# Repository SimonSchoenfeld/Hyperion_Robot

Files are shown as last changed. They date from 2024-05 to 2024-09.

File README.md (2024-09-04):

# Hyperion Roboter
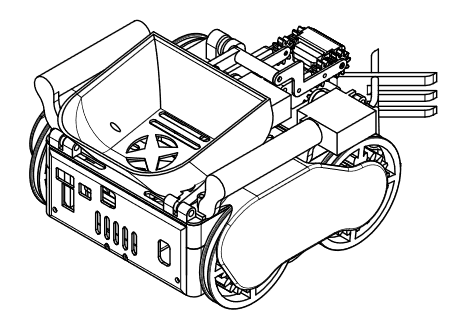
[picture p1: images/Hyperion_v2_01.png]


<br>
Dieses Repository enthält die Dokumentation des Hyperion Roboters, <br>
welcher von Simon Schönfeld für den Robocup Rescue Line Wettbewerb 2024 gebaut wurde. 

## Inhaltsübersicht
1. [Über mich](#über-mich)
2. [Regeln des Robocups](#regeln-des-robocups)
3. [Vorheriger Roboter](#vorheriger-roboter)
4. [Planung Hyperion v2](#planung-hyperion-v2)
   - [Platinen](#platinen)
   - [Das Fahrwerk](#das-fahrwerk)
   - [Das Gehäuse](#das-gehäuse)
   - [Die Kamera](#die-kamera)
   - [Schleifkontakte](#schleifkontakte)
   - [Greifarm](#greifarm)
5. [Funktionen](#funktionen)
   - [Linefollowing](#linefollowing)
   - [Kreuzungen](#kreuzungen)
   - [Hindernisse](#hindernisse)
   - [Rescue Area](#rescue-area)
6. [Probleme](#probleme)
7. [Fazit](#fazit)
8. [Zusätzliche Ressourcen](#zusätzliche-ressourcen)

## Über mich
Mein Name ist Simon Schönfeld, ich besuchte seit der 5ten Klasse die Informatik AG meiner Schule. Ziel dieser AG war es, Lego Roboter zu bauen, welche einer Linie folgen, um mit diesen dann einmal im Jahr beim Robocup Wettbewerb teil zu nehmen. 
Obwohl ich es nie geschafft habe, mich mit einem Lego Roboter für die deutschen Meisterschaften des Robocup zu qualifizieren, beschloss ich mich während der Coronapause gemeinsam mit meinem damaligen Teamkameraden, dazu, einen eigenen Roboter zu bauen. 

## Regeln des Robocups
Die Roboter beim Robocup müssen einen Parkour absolvieren, welcher aus einer Schwarzen Linie und einer "Rescue Area" besteht. Der Roboter muss der Schwarzen Linie folgen und dabei verschiedene Hindernisse überwinden. Diese Hindernisse bestehen aus Bumpern, Blockaden und Lücken. An Kreuzungen befinden sich zudem grüne Maskierungen, welche die Roboter erkennen und abhängig von der Position des Punktes drehen müssen. Die Rescue Area wird mit einem Silbernen Streifen eingeleitet. In ihr kann der Roboter Kugeln in verschiedene Ecken befördern, um Zusatzpunkte zu bekommen. Schwarze Kugeln müssen in die rote Ecke, die Silbernen Kugeln müssen in die grüne Ecke.

Die genauen Regeln befinden sich [hier](https://junior.robocup.org/wp-content/uploads/2024/04/RCJRescueLine2024-final-1.pdf).
<br>
<br>
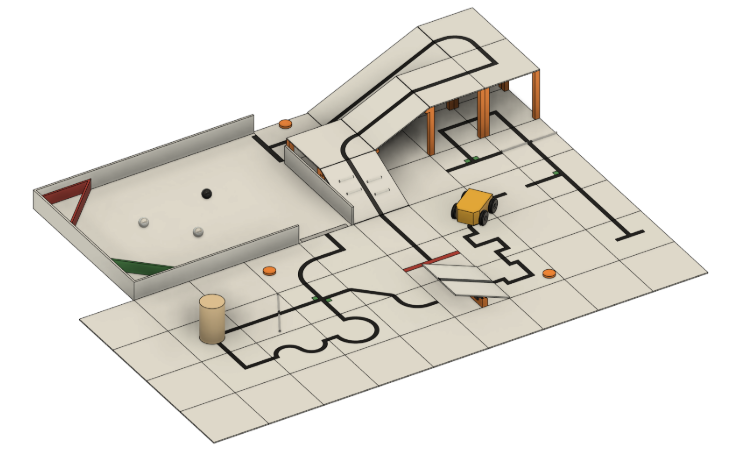
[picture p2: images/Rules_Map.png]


## Vorheriger Roboter
Obwohl ich es nie geschafft habe, mich mit einem Lego Roboter für die deutschen Meisterschaften des Robocup zu qualifizieren, beschloss ich mich während der Coronapause gemeinsam mit meinem damaligen Teamkameraden, dazu, einen eigenen Roboter zu bauen. Zu diesem Zeitpunkt war ich zwischen 14 und 15 Jahre alt und wusste so gut wie gar nichts über Elektronik und dem Erstellen von 3D Modellen, lediglich mit dem Programmieren hatte ich mich bereits länger beschäftigt. 
Da sich zu der Zeit auch Niemand in der AG damit auskannte, waren wir mehr oder weniger auf uns alleine gestellt und brauchten bereits mehrere Monate um zum ersten Mal zwei Schrittmotoren zu verwenden. Ich nahm den Roboter mehrfach mit nach Hause und baute und testete ihn dort ausgiebig. 
Als wir schließlich mit dem Roboter angetreten sind, versagte er vollkommen auf Grund von vielen unterschiedlichen Problemen. Dennoch habe ich in diesem Jahr so viel gelernt wie nie zuvor und beherrschte nun Grundkenntnisse in Schaltkreisen, 3D modellieren mit Fusion 360 und der Gesamtmechatronik eines Roboters. Da der Roboter meinem Teammitglied über die Zeit deutlich zu komplex und zeitintensiv wurde baute und programmierte ich ihn fast vollständig alleine und nach dem Wettbewerb verließ er die AG.

>[!NOTE]
> Wenn es darum geht im Robocup zu gewinnen, ist das Bauen eines eigenen Roboters absolut kontraproduktiv. Die Lego Roboter sind inzwischen so ausgereift, dass sie um Welten genauer und simpler sind. Die Gewinner des Robocups sind fast ausschließlich Lego Roboter und auch in den Qualifikationsrunden, an denen ich teilgenommen habe bin ich bis jetzt immer der Einzige Teilnehmer mit einem 100% selbstgebauten Roboter gewesen. Ich baue dennoch einen eigenen Roboter, da es mir nicht um das Gewinnen, sondern um die Herausforderung geht und darum, neue Dinge zu lernen. 

## Probleme des ersten Roboters

- Der Roboter basierte auf einem Fahrwerk eines Schülers, welcher schon vor mehreren Jahren die Schule verlassen hatte. Er hat sich damals mit seinem selbstgebauten Roboter für die deutsche Meisterschaft qualifizieren können. Der Roboter befand sich zu großen Teilen noch im Besitz der AG, weshalb wir das Fahrwerk als Grundbaustein nutzen und über die Zeit immer weiter veränderten. Am Ende war zwar nur noch die verwendete Kette ein Originalteil, dennoch haben wir die Ursprungsmaße nie verändert. Der Roboter war zu klein und Schmal, um noch mehr Bauteile unter zu bringen. Somit bestand der Roboter lediglich aus den Motoren und Treibern, sowie den Farbsensoren, Arduino und Akku. Später fügten wir zudem ein Greifarm hinzu.
<br>
<br>


- Aufgrund der Bauweise war es sehr schwierig an das Innere des Roboters zu kommen, weshalb man ihn ständig auseinander bauen musste. Die Kabel waren zudem alle weiß und rot, was schnell zu Verwirrung führte. Der später hinzugefügte Greifarm war sehr schlecht konstruiert und passte nicht wirklich zum Fahrwerk. All dies führte dazu, dass das Finden und Beheben von Fehlern sehr zeitaufwändig gewesen ist. Zudem gab es keine Möglichkeiten die Kugeln überhaubt zu finden oder die Rescue Are überhaubt zu lokalisieren. 
<br>
<br>
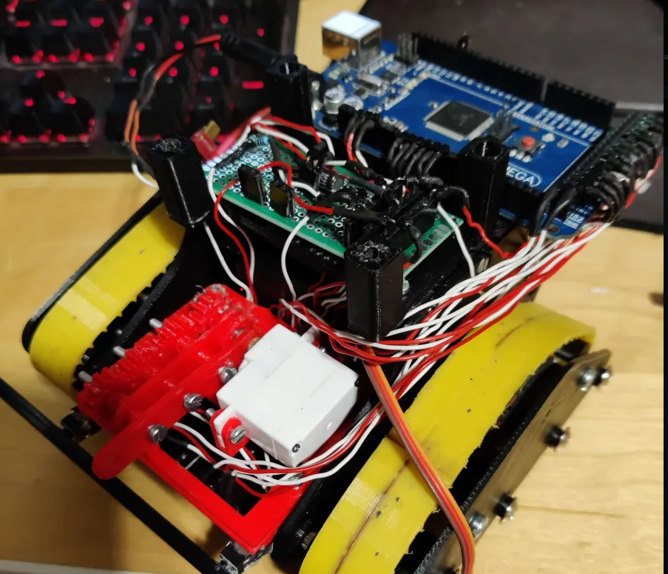
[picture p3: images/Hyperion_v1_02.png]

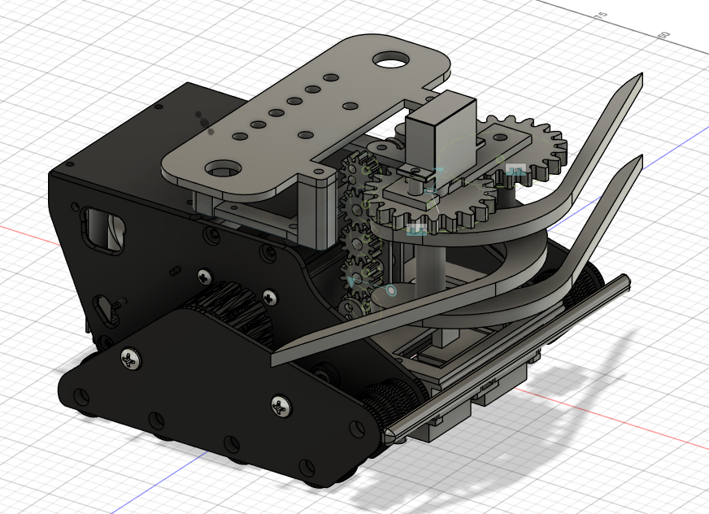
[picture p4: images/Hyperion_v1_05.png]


- Die Kette war nicht rutschfest genug, wodurch der Roboter auf Steigungen wiederholt abrutschte. Die Räder unter den Ketten haben sich zu dem bei zu großer Belastung selber festgezogen und sind regelmäßig blockier, da sie auf Schrauben montiert waren. Die hohe Anzahl an kleinen Bauteilen hat zudem dafür gesorgt, dass an dem kleinen Roboter über 100 Schrauben verbaut waren. Dies machte ihn sehr schwer. Dieses Problem und dadurch, dass die Schrittmotoren sehr ineffizient angesteuert wurden, sorgte dafür, dass der Roboter sich kaum bewegen konnte. 
<br>
<br>
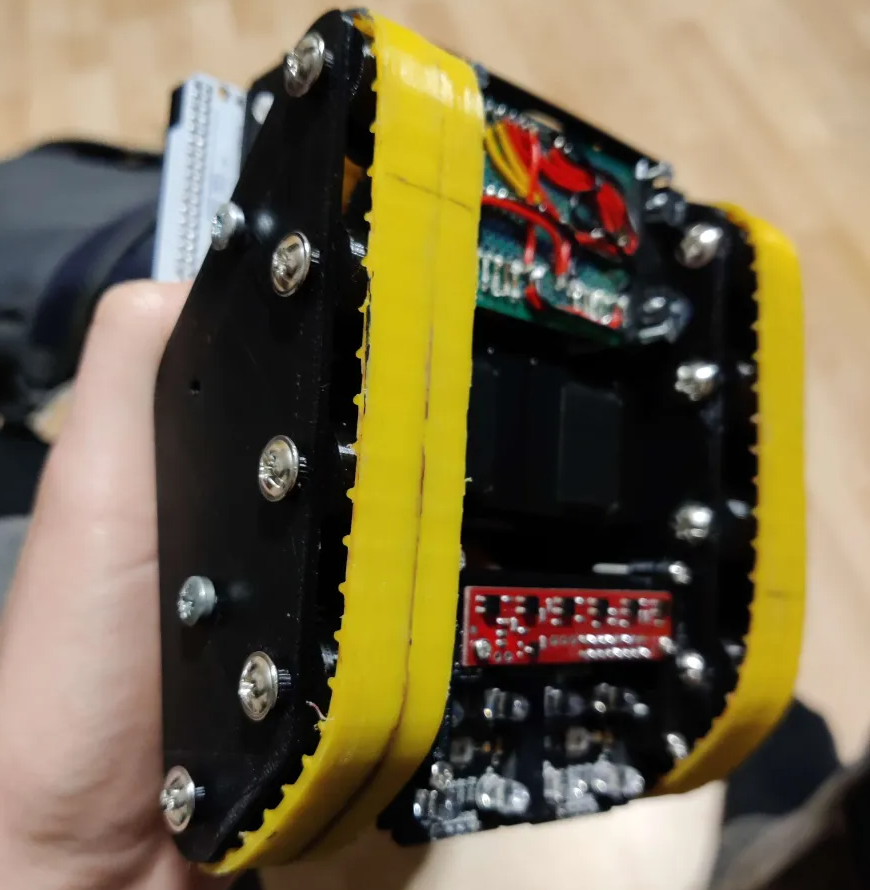
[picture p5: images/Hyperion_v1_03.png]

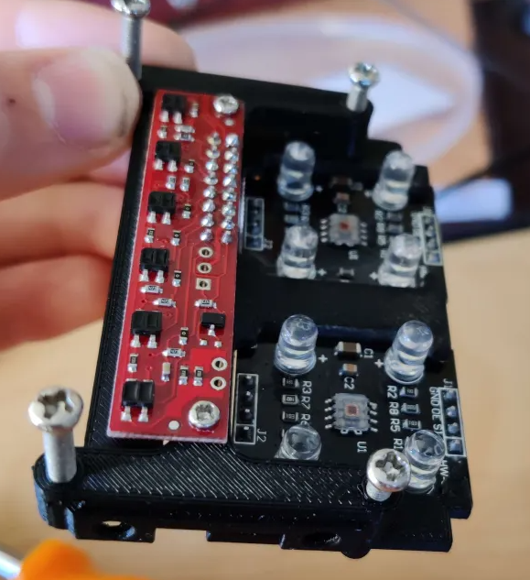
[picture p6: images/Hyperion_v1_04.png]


- Wenn es darum ging einer einfachen Linie zu Folgen hat der Roboter sehr präzise funktioniert. Dennoch gab es immer wieder Probleme welche schnell dazu führten, dass der Roboter gar nicht mehr funktionierte. Und auch das Erkennen der Kreuzungen funktionierte nur selten, da die Farbsensoren zu ungenau waren und sehr genau kalibriert werden mussten. (Dies liegt auch an dem speziellen Grünton der Punkte)
<br>
<br>

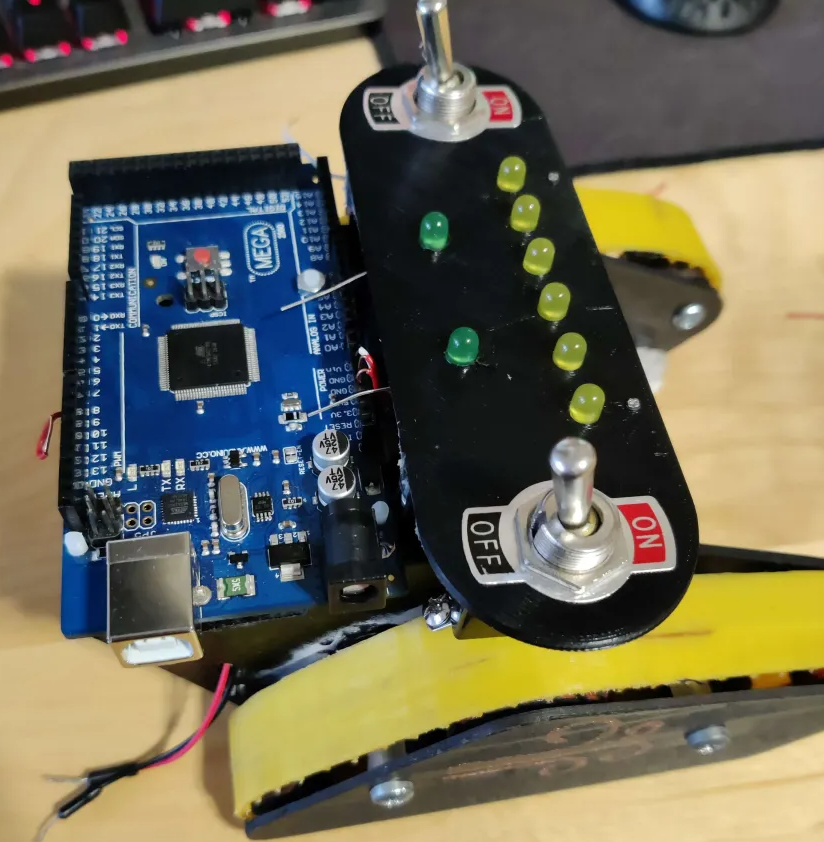
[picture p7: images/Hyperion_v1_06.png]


<br>
<br>
<br>

# Planung Hyperion v2
<br>

## Platinen
Statt einem Arduino Mega soll nun ein Raspberry Pi verwendet werden. Dieser ermöglicht es eine Kamera zu verwenden, um die Kugeln zu finden. Zudem ermöglicht er das Nutzen von Multiprozessen. Zudem kann der Roboter nun kabellos programmiert werden und ist insgesamt leistungsfähiger. Damit der Roboter einfach auseinandergebaut werden kann bedarf es mehrer Platinen, welche verschiedene Aufgaben erfüllen. Diese Platinen sind wiederum mit angesteckten Kabeln verbunden. Somit sind keine Bauteile permanent miteinander verbunden und lassen sich leicht zerlegen. 

### Analog-Digital-Wandler
Da die Grünen Punkte an den Kreuzungen durch die Kamera erkannt werden können, benötigt der Roboter lediglich die Grayscalesensoren zum Erkennen der Linie und ein Ultraschallsensor, welcher Hindernisse auf der Fahrbahn erkennen soll. Leider kann der Raspberry Pi die analogen Werte der Farbsensoren nicht selber auslesen, wie es der Arduino getan hat. Aus diesem Grund wird ein Analog zu Digital Wandler benötigt. Genutzt werden zwei MCP3008 Chips mit je 8 Inputs. Diese können über den SPI Bus mit dem Raspberry Pi verbunden werden und befinden sich auf der ersten Platine. Da die Anzahl an Analogen Inputs nicht mehr von den Anschlüssen des Raspberry Pis abhängig ist, sondern rein von der Anzahl an Wandlern, können gleich zwölf Grayscale Sensoren verwendet werden, wobei trotzdem noch vier Anschlüsse offenbleiben. Eine hohe Anzahl an Sensoren ermöglicht es die Linie in einer großen Fläche lokalisieren zu können. Zudem wird der Einfluss eines einzelnen, eventuell fehlerhaften Sensors reduziert. 
<br>
<br>
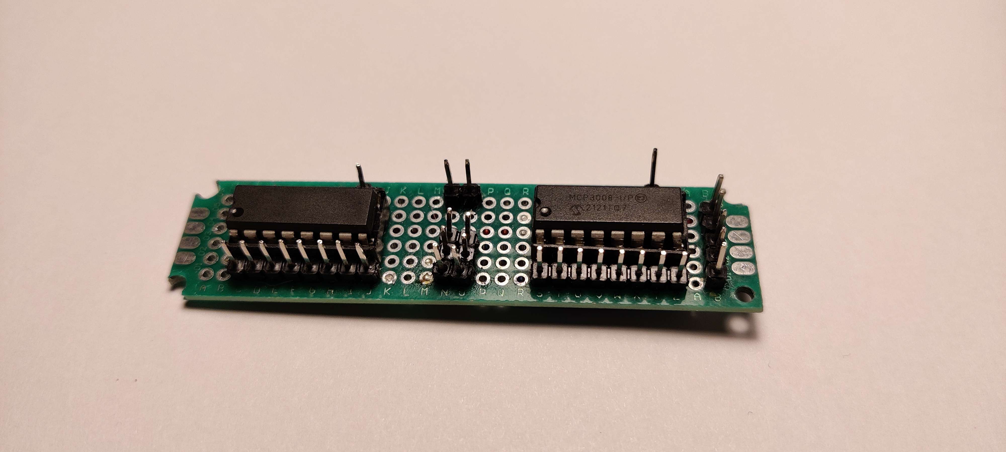
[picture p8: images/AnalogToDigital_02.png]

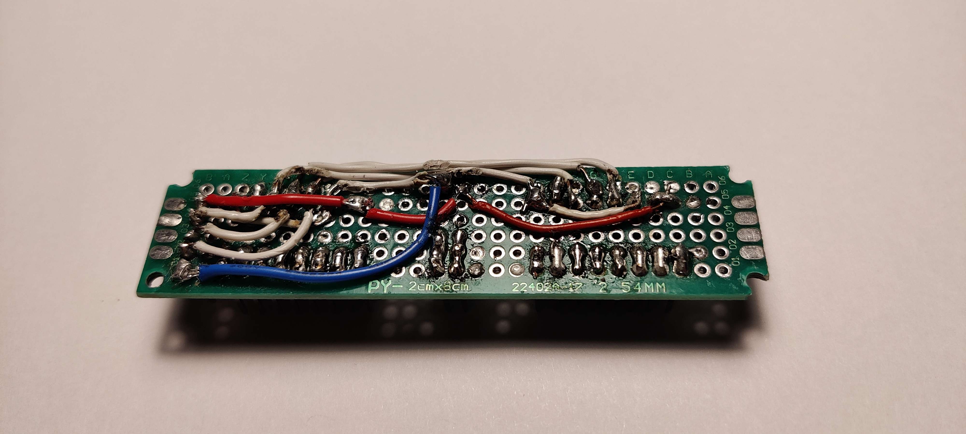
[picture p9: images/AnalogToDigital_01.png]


### Stromversorgung
Für die Schaltung werden zwei verschiedene Spannungen benötigt. 12V für die Motoren und 5.1V für den Raspberry Pi. Der Raspberry Pi hat zudem einen 3.3V Pin-Ausgang. Als Stromquelle wird ein 3S 12V LiPo Akku verwendet. Ein Aufwärtswandler bringt diese 12V auf 5.1V, welche über eine Verteilerplatine auf ein USB-Slot geleitet werden. Über ein kurzes USB-Kabel kann so der Raspberry Pi versorgt werden. Wenn man ein externes USB-Kabel verwendet, kann der PI auch angeschaltet und programmiert werden ohne dass die Motoren verbunden sind. An dem Akku befindet sich zudem ein Schalter, um den gesamten Strom abzuschalten und ein Modellflugzeug-Alarm, damit der Akku nicht vollständig entladen wird (und kaputt geht). 
<br>
<br>
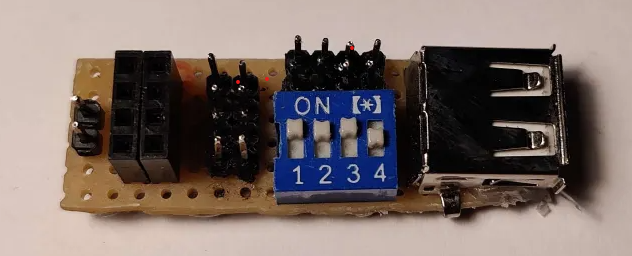
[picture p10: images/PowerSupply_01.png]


### Motortreiber
Um die Schrittmotoren ordnungsgemäß bedienen zu können bedarf es an einem Motortreiber für jeden Motor. Um diese Treiber richtig verwenden zu können müssen sie richtig verkabelt werden. Diesen vergleichsweisen komplexen Schaltkreis hatte ich zu Beginn des Projektes noch wie alle anderen Platinen von Hand gelötet. Als ich jedoch schließlich von "a4988" Treibern auf "drv8825" Treiber umgestiegen bin, musste ich eine Änderung an dem Schaltkreis vornehmen. Da die Platine nicht besonders gut verlötet war und die Rückseite der Platine bereits sehr unordentlich geworden ist, entschied ich mich für eine neue Platine. Um es einmal zu testen und mir gleichzeitig das Löten zu sparen, designte ich die Platine digital und ließ sie von einem Online Service herstellen. Das Ergebnis ist deutlich professioneller und weniger anfällig für Schäden als die von Hand gelötete Platine.
<br>
<br>
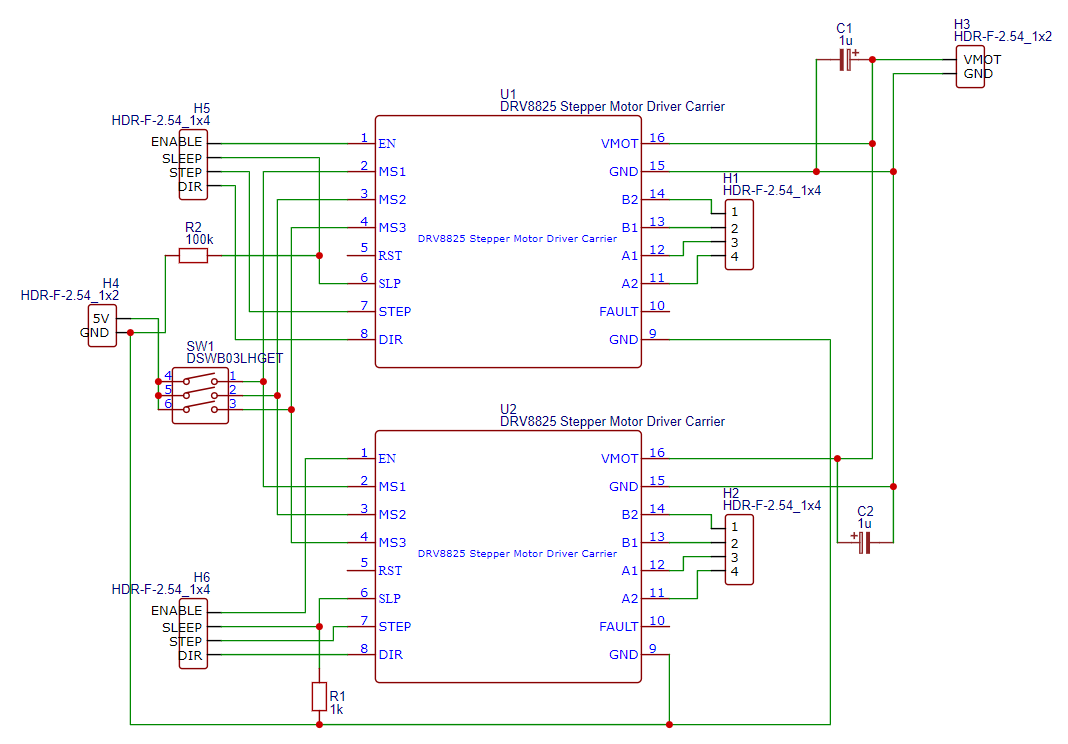
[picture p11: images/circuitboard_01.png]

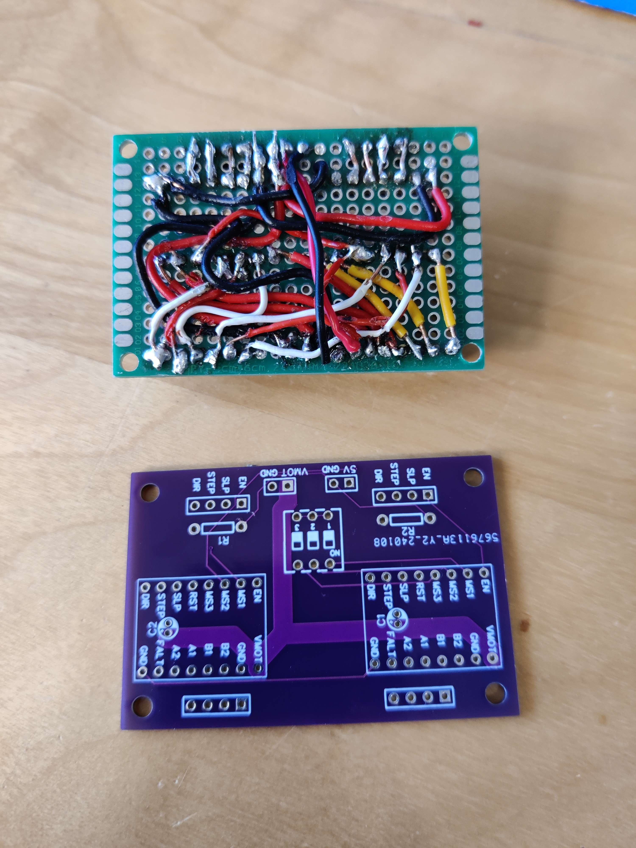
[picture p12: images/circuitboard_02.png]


### Knöpfe
Der Roboter muss während des Robocup Wettbewerbes mehrfach von der Fahrbahn genommen werden und an einer anderen Stelle neu gestartet werden. Um den Roboter zu starten und zu stoppen, bedarf es eine Möglichkeit für Manuelle Inputs, da der Roboter während des Wettbewerbes nicht über WLAN verbunden sein darf. Aus diesem Grund befinden sich an der Rückseite des Roboters zwei Knöpfe für mögliche Eingaben und zwei LEDs zur Statusanzeige. 
<br>
<br>

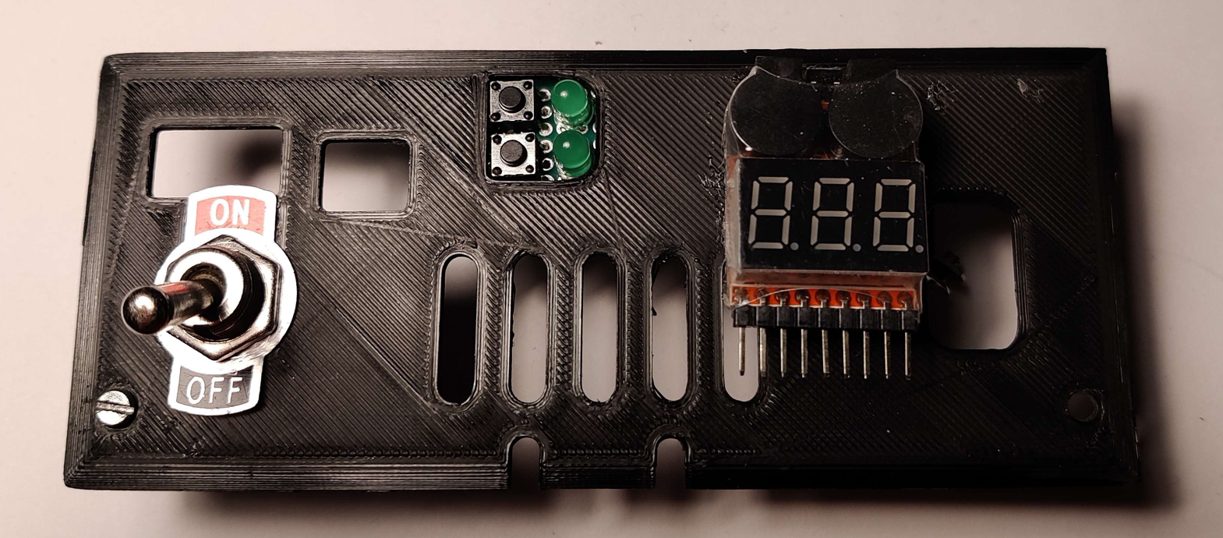
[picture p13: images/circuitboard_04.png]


### Verteiler
Damit die einzelnen Teile des Roboters einfach und schnell zu verkabeln, empfiehlt es sich breite Stecker zu verwenden, sodass jeweils nur ein Kabelstrang eingesteckt werden muss. Um die Signale auf die richtigen Kabel zu leiten gibt es eine Verteilerplatine, welche sich unter dem Raspberry Pi befindet. Mit ihr ist sowohl die obere Hälfte des Roboters als auch die abnehmbare Heckplatte verbunden. 
<br>
<br>
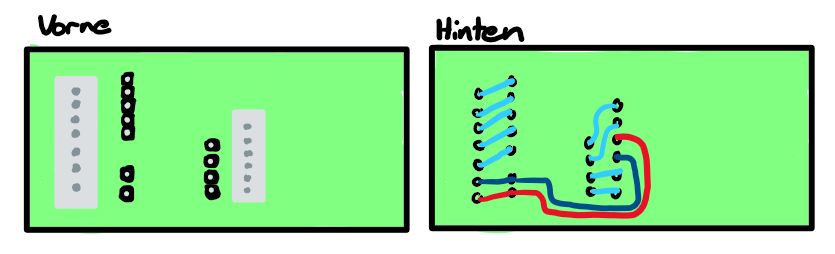
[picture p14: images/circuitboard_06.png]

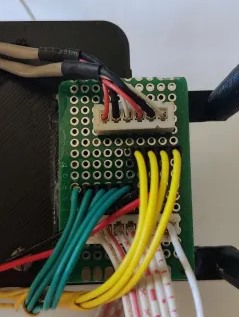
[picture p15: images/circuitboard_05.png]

 
 ### Servo Motoren
An der oberen Hälfte des Roboters befinden sich fünf Servo Motoren sowie einen Lüfter. Um diese Bauteile korrekt zu verbinden und dabei nur einen Stecker zu verwenden wird ebenfalls eine Platine verwendet. Zudem befindet sich an dieser Platine ein weiterer Stecker um zwei helle LEDs an der Vorderseite des Roboters mit Strom zu versorgen.
<br>
<br>
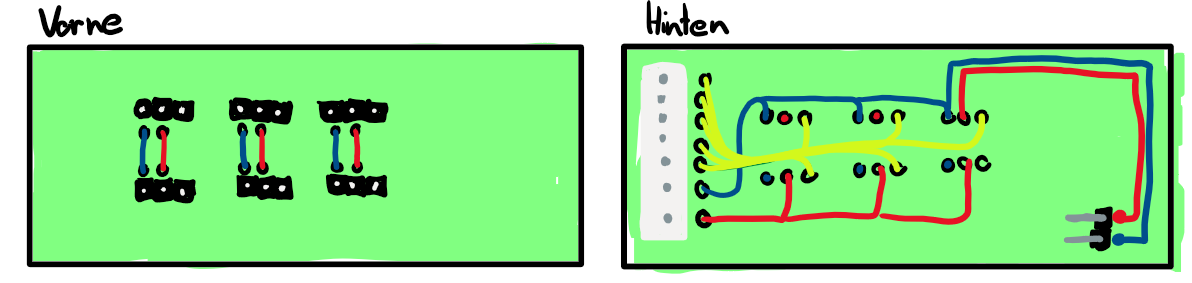
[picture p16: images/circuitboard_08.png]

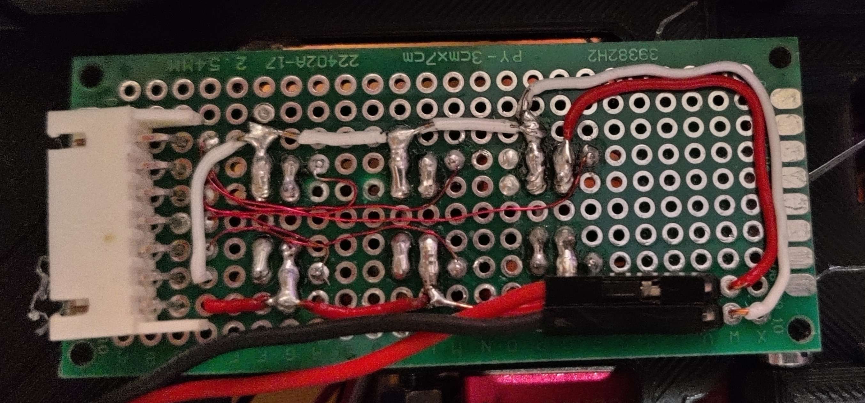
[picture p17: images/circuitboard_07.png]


## Das Fahrwerk
Die meisten Probleme des ersten Roboters entstanden durch das Fahrwerk. Jeder Versuch, eine neue Kette auszudrucken scheiterte, weshalb wir keine Möglichkeit hatten den Roboter zu vergrößern. Die genutzte Kette war sehr glatt und haftete nur schlecht an dem Boden. Um diese Probleme zu vermeiden, nutzt der neue Roboter vier Räder. Die Räder haben einen Durchmesser von 90cm, welches das Überqueren von Bumpern deutlich erleichtert. Um genügend Haftung zu erreichen, werden um die Räder Herum Aktengummibänder geklebt. Diese haben die perfekte Größe und Breite und haften super an glatten Oberflächen.
Damit der Roboter trotz der großen Räder nicht zu schnell fährt und beim Fahren mehr Kraft hat, werden die Räder mit einer Zahnradübersetzung von 15 zu 20 angetrieben. Das kleinere Zahnrad sitzt dabei in der Mitte zwischen den beiden Rädern und ist direkt mit der Motorachse verbunden. Dadurch befinden sich die schweren Motoren genau in der Mitte des Roboters. Die Räder sitzen dabei in Kugellagern, weshalb nur wenig Reibung entsteht. 
<br>
<br>
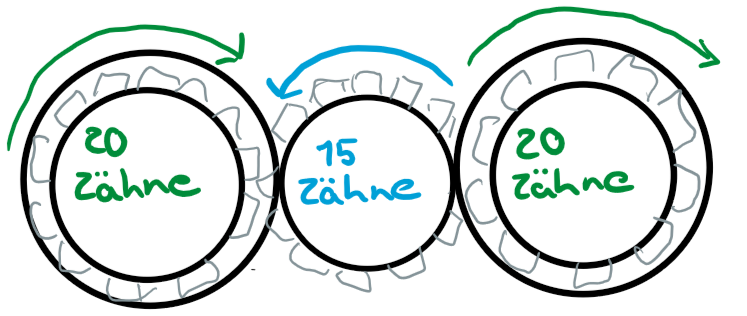
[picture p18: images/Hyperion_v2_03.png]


## Das Gehäuse
Eine große Änderung des Roboters ist das Gehäuse. Es bietet den Grundstein für den gesamten Roboter. Ein großer Unterschied zum Vorgänger ist, dass das Gehäuse dieses Mal aus einem großen, einzelnen Stück besteht. In ihm soll die gesamte Elektronik untergebracht werden können und gleichzeitig schnell zu erreichen sein. Damit später alles passt, wurde die Elektronik bereits vorher ausgewählt und getestet, um jedem Bauteil einen festen Platz zu geben. Die Motoren bilden zusammen mit ihren Treibern ein einzelnes Modul, welches sich entfernen lässt, um einfacher an den Motoren arbeiten zu können. Der Mittlere Teil des Roboters besteht also aus den Motoren. Im vorderen Teil befinden sich die Sensoren und im hinteren Teil der Spannungswandler, der Akku und die Platine mit den Analog zu Digital Wandlern. Der Raspberry Pi selber befindet sich auf einer separat abnehmbaren Platte über dem LiPo Akku.
<br>
<br>
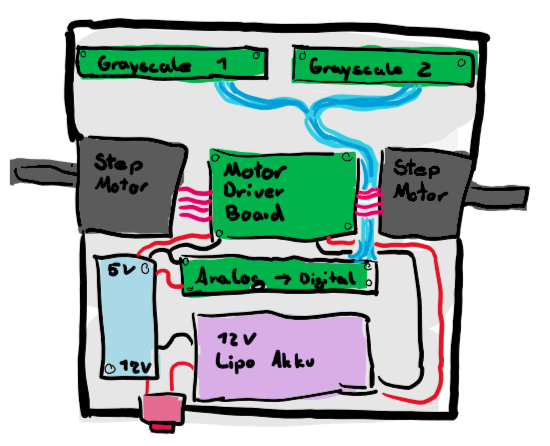
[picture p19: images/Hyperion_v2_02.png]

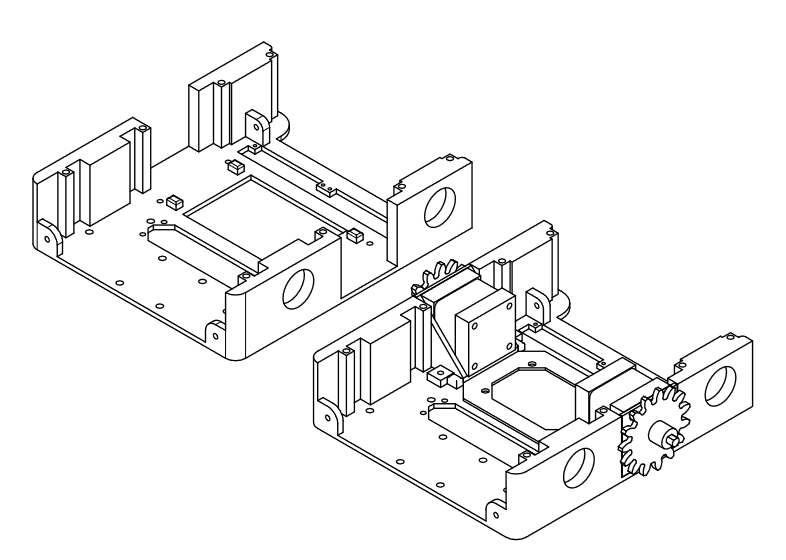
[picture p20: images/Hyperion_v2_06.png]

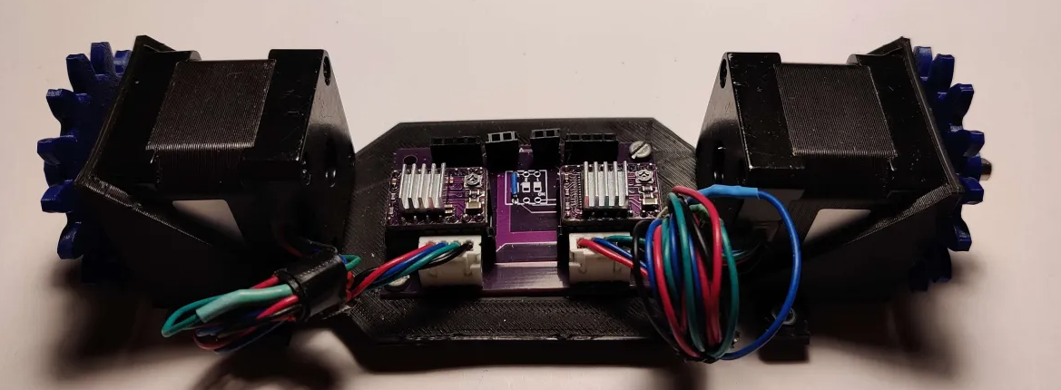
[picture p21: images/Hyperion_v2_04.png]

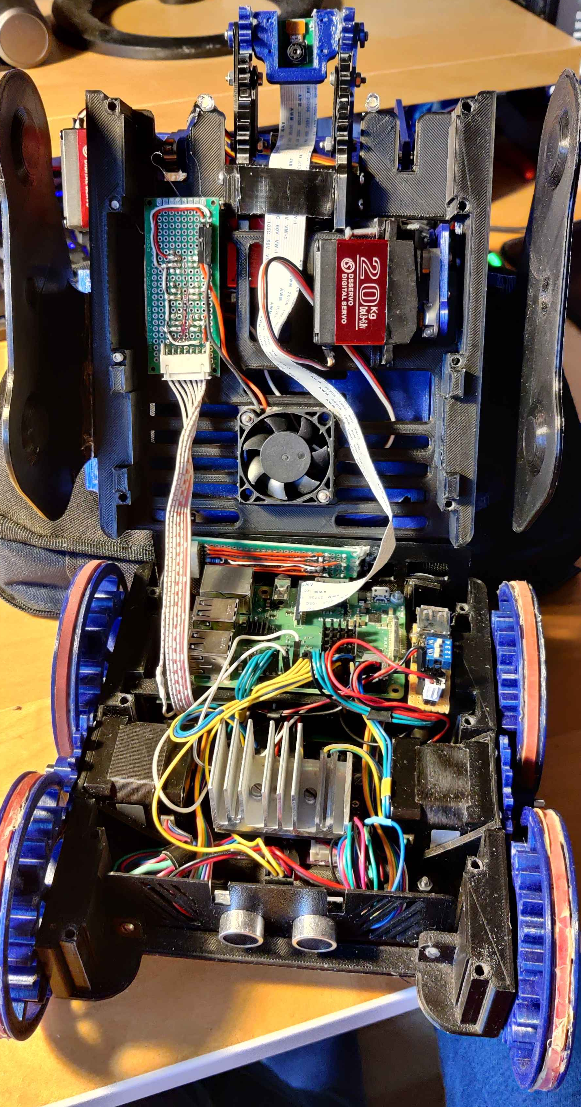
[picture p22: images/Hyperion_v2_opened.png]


## Die Kamera 
 Die Kamera soll beim Befahren des Kurses senkrecht nach unten gerichtet sein, um mögliche Kreuzungen zu erkennen. Wenn der Roboter jedoch die entsprechende Maskierung überfährt, muss die Kamera nach vorne gerichtet werden, damit die Kugeln von dem Roboter gefunden und aufgesammelt werden können. Um den Komplikationen eines doppelten Kamerasystems aus dem Weg zu gehen, wird eine einzelne Kamera mit Hilfe eines Servo Motors in die Richtige Position gedreht. Damit die Ausrichtung stimmt werden zudem mehrere Zahnräder genutzt. 
<br>
<br>
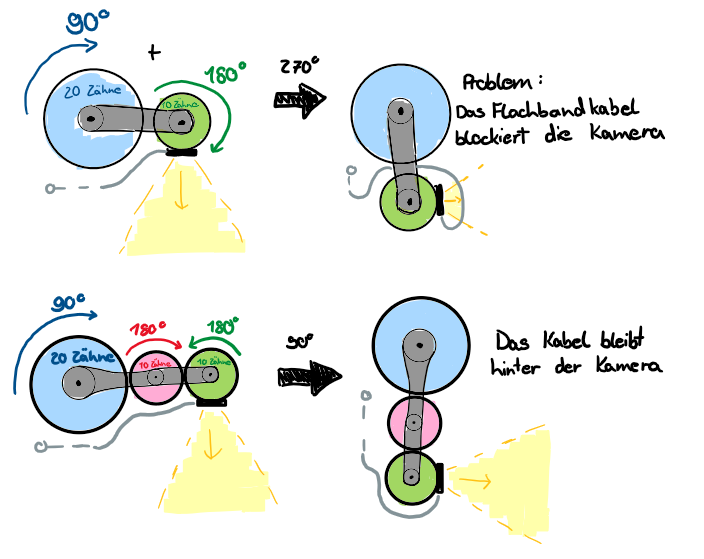
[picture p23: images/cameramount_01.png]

<br>

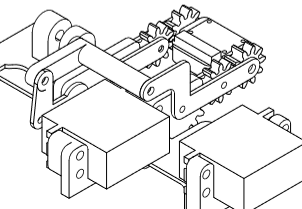
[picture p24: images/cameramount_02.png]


## Schleifkontakte
Damit der Roboter überhaubt Kugeln finden und später einsammeln kann, muss er zuerst die "Rescue Area" finden. Diese beginnt mit einem silbernen Streifen auf der Fahrbahn. Da das Erkennen von Reflektieren von reflektierenden Oberflächen sowohl für die Sensoren als auch für die Kamera zu Komplikationen führen kann, macht der Roboter von einer weiteren (vermutlich unabsichtlichen) Eigenschaft des Streifens gebrauch. Der silberne Streifen leitet Strom und kann daher mit zwei Schleifkontakten erfasst werden. Danach kann sich der Roboter mit Hilfe der Kamera und des Ultraschall-Sensors in der "Rescue Area" zurechtfinden. 
<br>
<br>

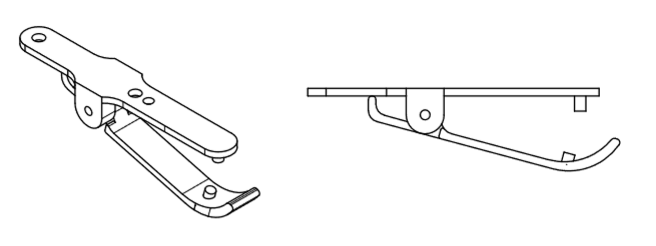
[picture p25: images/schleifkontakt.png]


## Greifarm
Um die Kugeln in der Rescue Area aufsammeln zu können benötigt der Roboter einen Greifarm. Dieser befindet sich während der normalen Fahrt oben auf dem Roboter. Er kann bei Bedarf kann der Greifarm dann heruntergeklappt werden und eine Kugel hochheben. Die Kugel wird dabei in eine Ladefläche gelegt, welche sich ebenfalls auf dem Roboter befindet. In dieser Ladefläche ist Platz bis zu vier Kugeln und sie kann nach hinten weg entleert werden. So kann auch die 6cm hohe Wand der roten und grünen Ecken überwunden werden, zu denen die Kugeln gebracht werden müssen. 
<br>
<br>

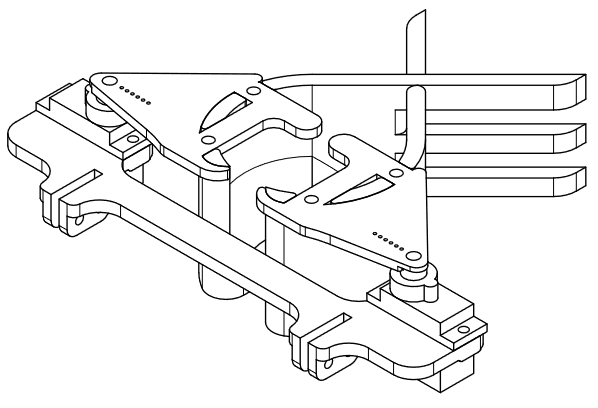
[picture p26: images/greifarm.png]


# Funktionen

## Linefollowing
Der wohl einfachste Teil der Programmierung ist der des Linefollowing. Üblicherweise verläuft das Folgen der Linie bei den Legorobotern nach einem bestimmten Prinzip. Sie besitzen einen Farbsensor links und einen rechts neben der Linie. Steht der Roboter gerade auf der Linie erkennt keiner der beiden Sensoren die schwarze Spur und der Roboter fährt geradeaus. Macht die Linie nun eine Kurve oder kommt der Roboter vom Weg ab, erkennt das der jeweilige Sensor und der Roboter kann seine Position korrigieren. Es kommt jedoch auch häufig vor, dass die Roboter in Endlosschleifen festhängen, wenn sie ungünstig auf der Linie stehen. 

Der Hyperion Roboter hat im Vergleich zu den Lego Robotern den Vorteil, dass er eine deutlich höhere Anzahl von Sensoren nutzen kann. Unter dem Roboter befinden sich also nicht nur zwei sondern gleich zwölf Graustufensensoren, welche die Linie in einem großen Bereich durch die unterschiedlichen Lichtverhältnisse erfassen können. Dies verhindert zum einen, dass der Roboter die Linie verliert und ermöglicht es, dass der Roboter seine Geschwindigkeit gleichmäßig zur Linienposition anpassen kann. Dadurch fährt er gleichmäßig und kommt nur selten ins Stottern. 

## Kreuzungen 
Um an Kreuzungen den richtigen Weg einzuschlagen, muss der Roboter in der Lage sein, grüne Punkte zu erkennen. Dies ist besonders mit den neueren Lego Minestorm Modellen keine Schwierigkeit, da die zugehörigen Sensoren Farben ohne Kalibrierung genau erkennen konnten. Dies ist mit klassischen Arduino-Sensoren deutlich schwieriger, weil sich die Lichtverhältnisse dauerhaft ändern und der Grünton in einem sehr dunkelblauen Spektrum liegt. Aus diesem Grund verwendet der Roboter eine Kamera, um die Kreuzungen zu erkennen. Wenn der Roboter jede Kreuzungsversion abgespeichert hat und erkennen könnte, würde er bei jeder Kreuzung eine vorprogrammierte Aktion abrufen können.

Der erste Ansatz bestand daraus, ein paar Bilder von jeder Kreuzung zu machen und mit dem aktuellen Kamerabild abzugleichen und auszumachen, ob es sich um welche Kreuzung es sich handelte. Diese Methode stellte sich aber als viel zu langsam heraus und spätestens, wenn der Roboter schräg auf der Linie Stand scheiterte das Programm.

Die finale Methode war deutlich komplexer als ein einfacher Vergleich von Bildern. Ich schrieb ein Programm, mit dem ich sehr viele Bilder über die Kamera in kurzer Zeit machen konnte. Damit machte ich von jeder Kreuzung Kategorisiert ca. 1000 Bilder, während ich den Roboter vor und zurück bewegte und drehte. Mit Hilfe dieser Bilder trainierte ich dann eine "KI" also ein simples neuronales Netzwerk, welches die einzelnen Varianten auseinanderhalten konnte. Nach sehr viel Fine Tuning mit Postprocessing und Belichtung konnte der Roboter mit diesem trainierten Modell nun relativ präzise die Kreuzungen erkennen.

## Hindernisse
Um die Wegblockaden zu erkennen, denen der Roboter ausweichen muss, ist in ihm ein Ultraschall-Sensor verbaut, welcher die Entfernung in Fahrtrichtung misst. Dieser Sensor sollte zudem ursprünglich bei der Orientierung in der Rescue Area helfen.

## Rescue Area
Nachdem der Eingang der Rescue Area von den Schleifkontakten erkannt wird, schaltet der Roboter in den Kugel-Sammel-Modus. Die Kamera wird heruntergeklappt, und schaltet auf ein Programm welche Kreise im Bild erkennt. Die erkannten Kugeln können zudem durch die Kamera nach Schwarz und Silber unterteilt werden und werden von dem Greifarm in den Sammelbecher gelegt. Danach sucht der Roboter mit der Kamera und dem Ultraschallsensor die passenden Ecken und liefert die Kugeln dorthin ab. Leider wurde das Programm für die Rescue Area nie zu Ende geschrieben. 

# Probleme

+ Der Roboter war leider ziemlich schwer und hatte somit Probleme die Rampen hinaufzufahren.
+ Die Schrittmotoren waren etwas zu schwach, um immer präzise Bewegungen auszuführen.
+ Die Motoren wurden teilweise so heiß, dass die Achse die PLA-Zahnräder geschmolzen hat und durchgerutscht ist.
+ Teilweise hat sich das Profile von den Rädern gelöst und in den Zahnrädern verfangen.
+ Weil die Kamera so weit vom Drehzentrum entfährt war, war sie nach Kurven nicht über der Linie
+ Die KI konnte zwar präzise Kreuzungen unterscheiden jedoch nie genau ausmachen, ob überhaubt eine Kreuzung vorhanden ist. 
+ Die Schleifkontakte konnten vorwärts zwar über Hindernisse gleiten, blieben aber beim Zurücksetzen hängen.
+ Im Gegensatz zu einem Arduino lässt der Raspberry Pi sich nicht mal eben neu starten. Wenn er abstürzt, ist der Lauf vorbei. 
+ Ich hatte am Ende zu wenig Zeit, um die Programmierung zu vervollständigen und alle Funktionen zu nutzen. 
+ Die einzelnen Funktionen funktionierten zwar, das zusammenhängende Programm hatte jedoch viele Fehler.

# Fazit

Im Robocup Wettbewerb konnte sich der Hyperion Roboter nicht für die deutsche Meisterschaft qualifizieren. Er scheiterte in jedem Lauf an unterschiedlichen Problemen und erreichte in keinem einzigem das Ziel. Dieses Ergebnis ist enttäuschend, war jedoch schon Wochen und Monate vorher vorherzusehen. Der Roboter war extrem overengineered und war in einem einzigen Jahr zu viel Arbeit für eine einzelne Person. Um bei dem Wettbewerb eine Chance zu haben, sollte man Lego Bauteile Nutzen und möglichst gemeinsam an Problemen arbeiten. Dass meine Herangehensweisen und Methoden eher unpraktisch waren war mir von Anfang an Bewusst. Es ging mir allerdings auch weniger um das Gewinnen als darum neue Lösungsansätze für Probleme auszuprobieren, mit denen ich mich schon seit der 5ten Klasse beschäftige. In einzelnen Bereichen war der Roboter extrem präzise und hat super funktioniert und auch ohne den Wettbewerb hätte ich mich warscheinlich mit einem ähnlichen Projekt befasst. 

Durch das Hyperion Projekt habe ich extrem viel neues gelernt in Bereichen wie: 

+ Programmieren in Java und Python 
+ Die Bedienung vom Raspberry Pi inklusive Linux und SSH
+ Auswertung von Kamerabildern mit OpenCV 
+ Das Trainieren von KIs und deren Funktion
+ Die Funktion von unzähligen elektronischen Bauteilen
+ Das professionelle Design von Platinen
+ Elektronische Schaltungen 
+ Löten und Verkabeln
+ 3D Modellierung und Verwendung eines 3D Druckers
+ etc...

Auch wenn der Roboter unter den Letzen Plätzen des Wettbewerbes abgeschnitten hat, würde ich das Projekt allein schon aus diesem Grund jederzeit wiederholen.

>[!NOTE] 
>Sollte jemand Interesse an Weiteren Dateien, Teilelisten oder Infos haben, stelle ich das Gerne zur Verfügung. 

## Zusätzliche Ressourcen

- [vollständige Konstruktionszeichnung](assets/Zeichnung.pdf)
- [ansehbares 3D Modell](https://a360.co/3U4IwDF)
- [STL Dateien](assets/3d-model)

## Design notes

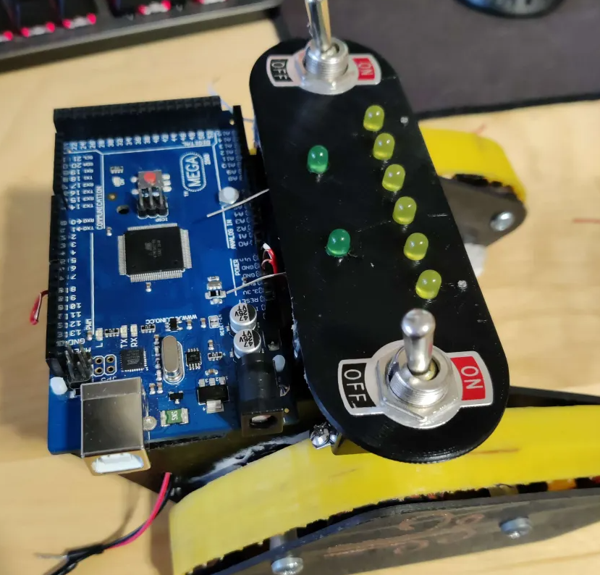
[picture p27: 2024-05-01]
images/Hyperion_v1_01.png

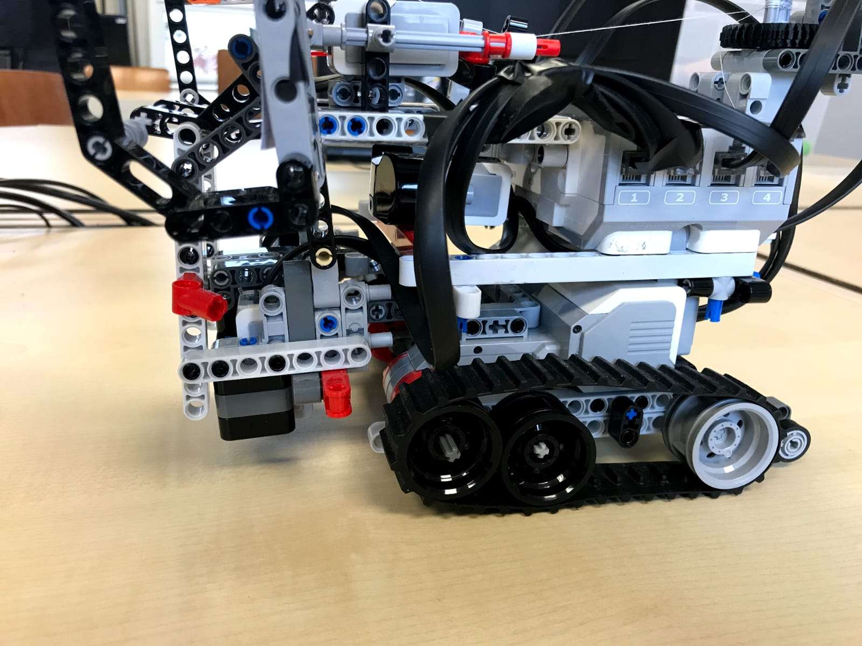
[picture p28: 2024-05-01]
images/Lego_Roboter.png

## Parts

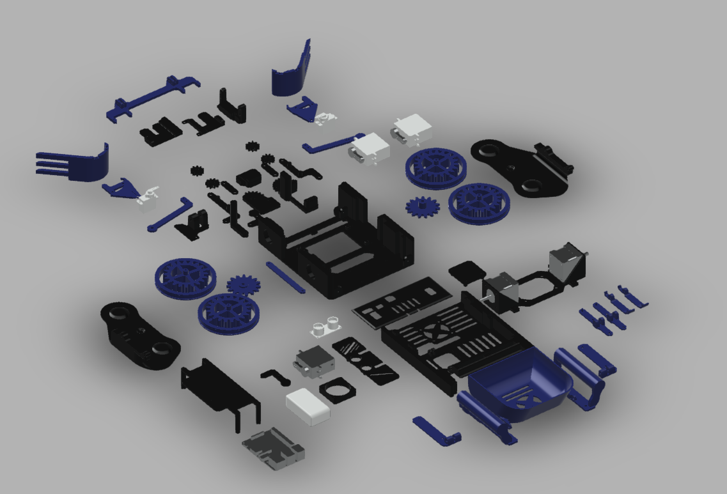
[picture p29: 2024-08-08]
images/parts.png

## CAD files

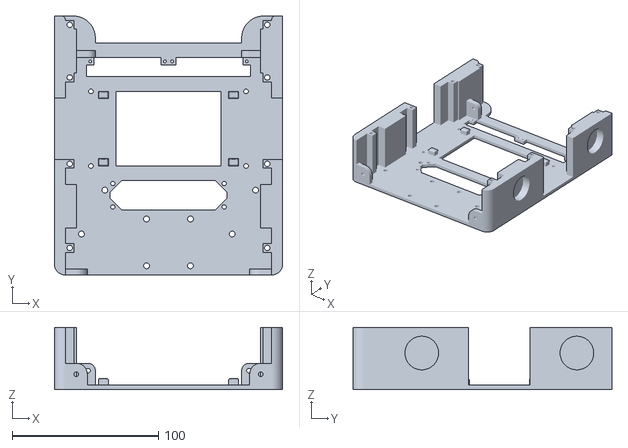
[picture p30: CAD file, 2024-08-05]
assets/3d-model/casing/mainFrame.stl
156.0 x 177.0 x 42.5

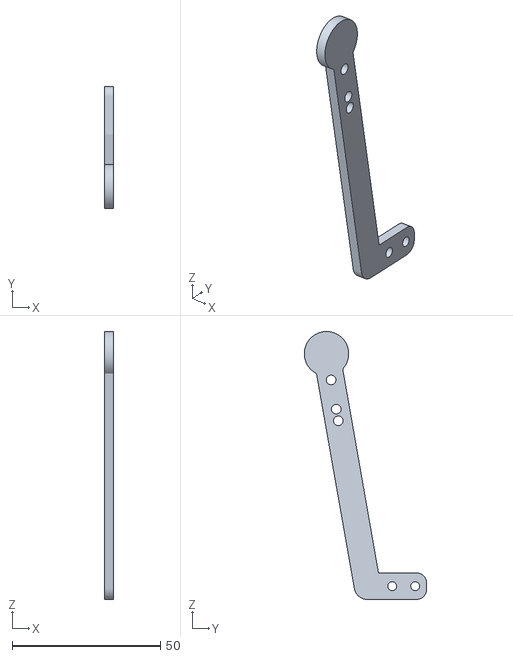
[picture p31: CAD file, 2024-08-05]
assets/3d-model/arm/arm_rod_right.stl
3.00 x 41.3 x 90.5

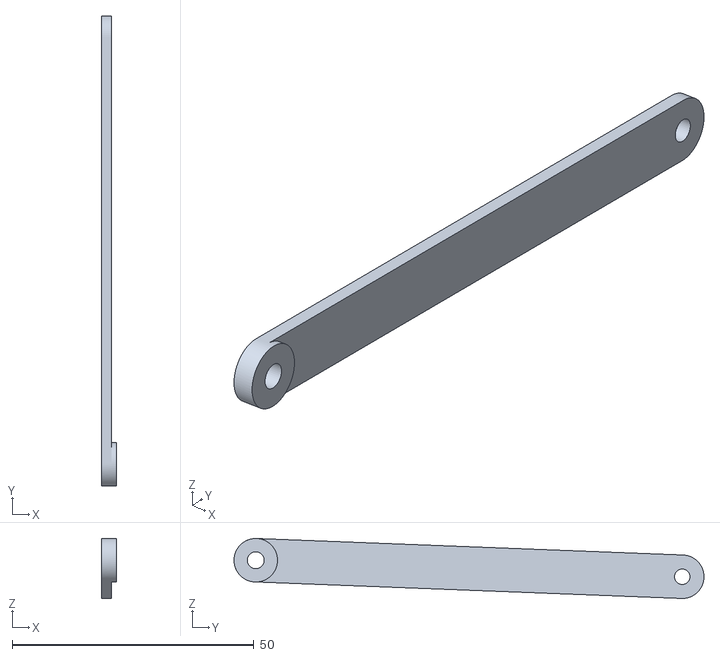
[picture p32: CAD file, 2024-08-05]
assets/3d-model/bucket/bucket_rod.stl
3.00 x 97.2 x 12.4

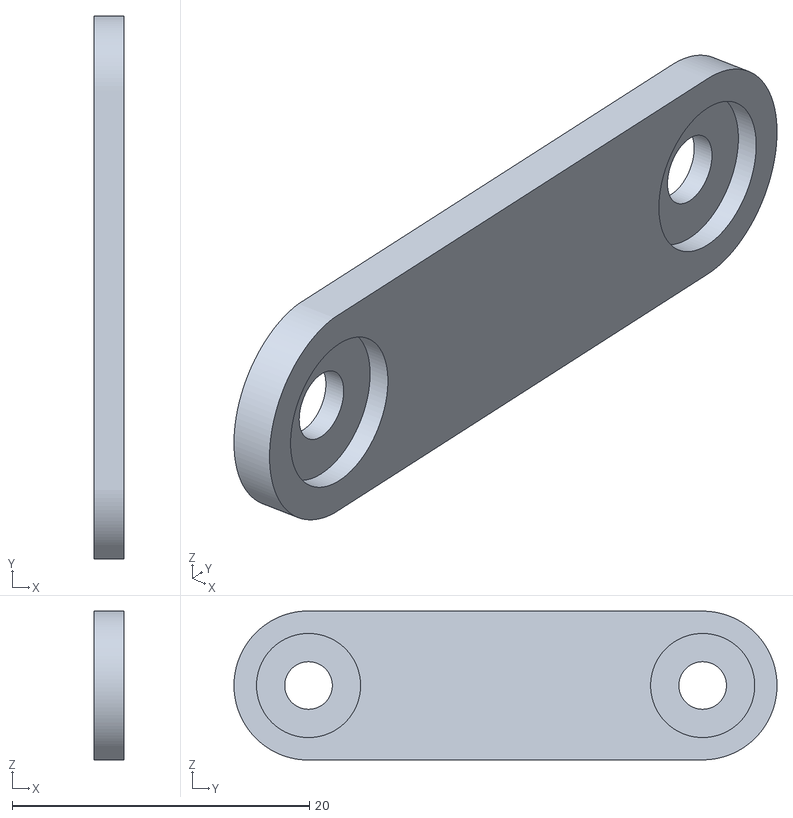
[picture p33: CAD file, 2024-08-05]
assets/3d-model/camera/camera_gearConnectorI_inside.stl
2.00 x 36.5 x 10.0

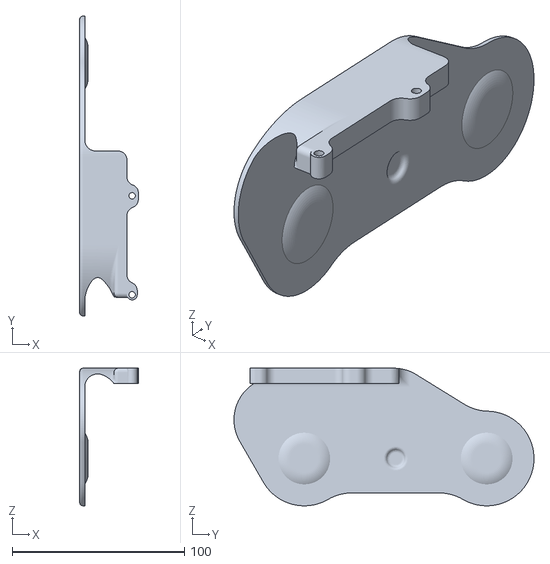
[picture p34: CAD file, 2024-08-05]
assets/3d-model/casing/frame_left.stl
34.1 x 174.4 x 80.0

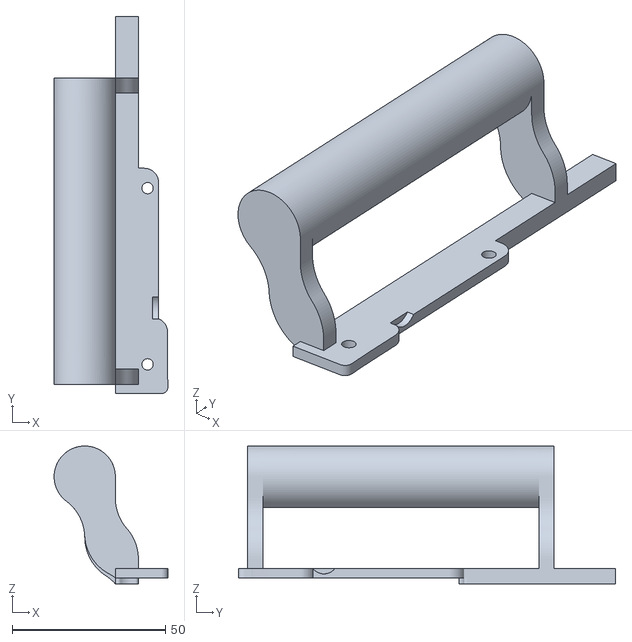
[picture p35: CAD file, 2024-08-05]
assets/3d-model/other/handle_left.stl
37.1 x 123.0 x 45.0

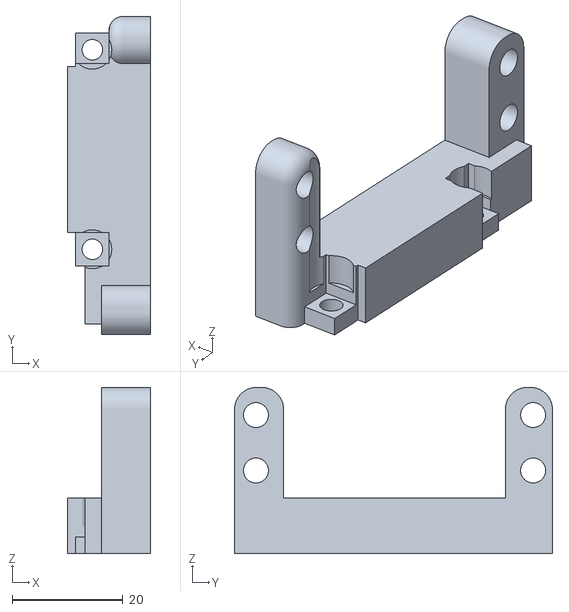
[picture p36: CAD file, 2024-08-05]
assets/3d-model/arm/arm_servoMount.stl
15.0 x 57.4 x 30.0

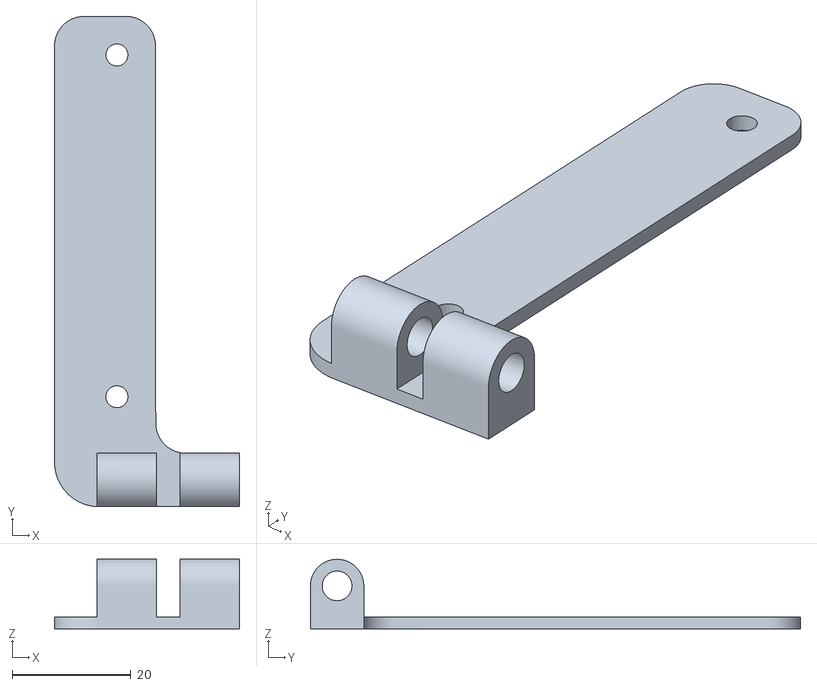
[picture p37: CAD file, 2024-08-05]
assets/3d-model/bucket/bucket_basePlate_left.stl
31.1 x 82.5 x 11.7

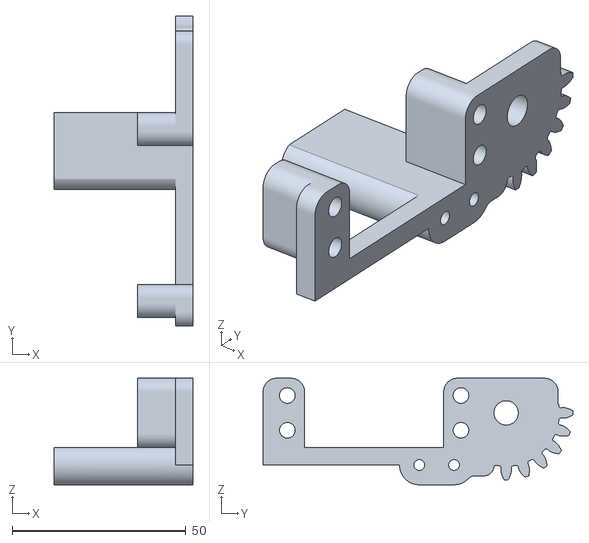
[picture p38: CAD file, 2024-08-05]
assets/3d-model/camera/camera_gearMount_right.stl
40.0 x 89.2 x 30.7

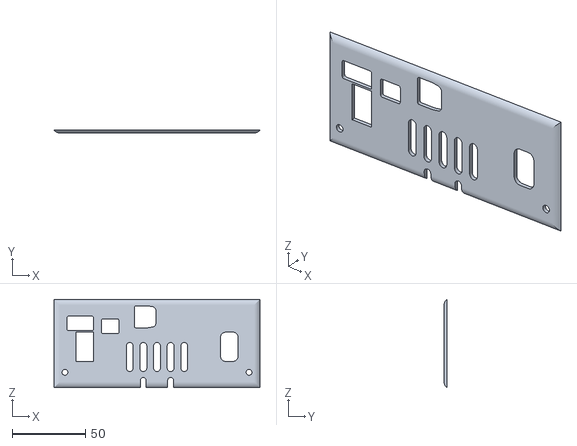
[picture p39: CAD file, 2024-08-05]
assets/3d-model/casing/backplate.stl
141.0 x 2.00 x 60.5

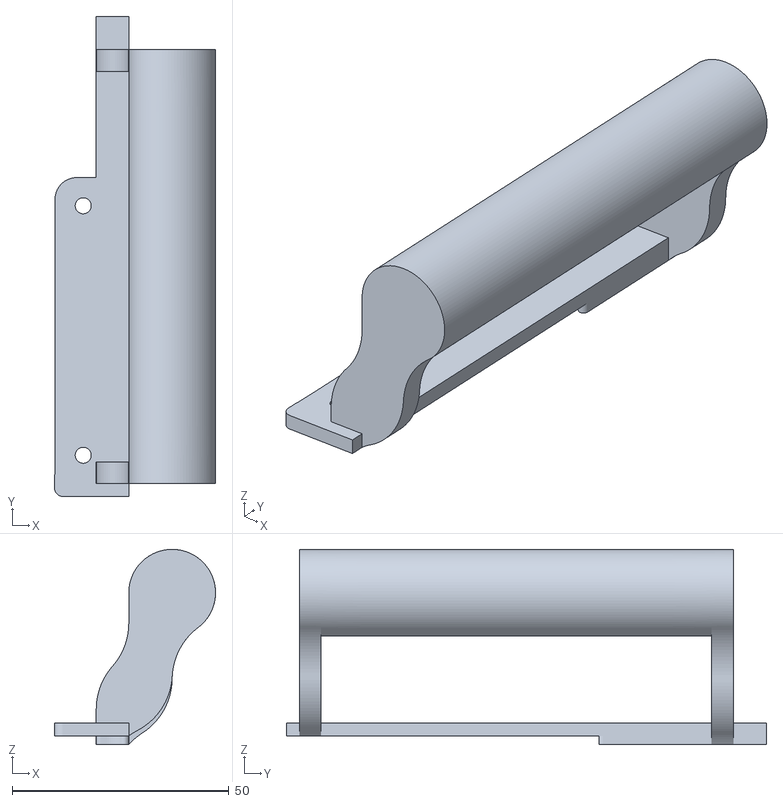
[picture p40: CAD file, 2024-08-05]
assets/3d-model/other/handle_right.stl
37.1 x 110.6 x 45.0

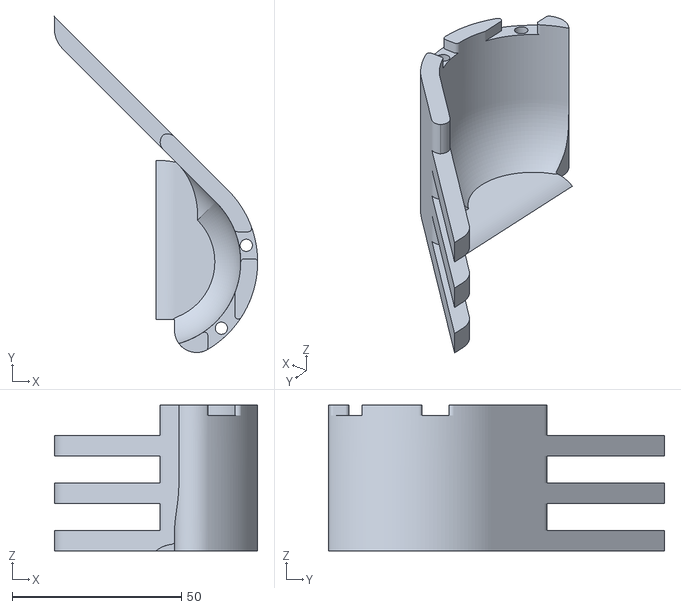
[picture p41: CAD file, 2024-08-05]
assets/3d-model/arm/arm_right_2.stl
60.0 x 99.1 x 43.0

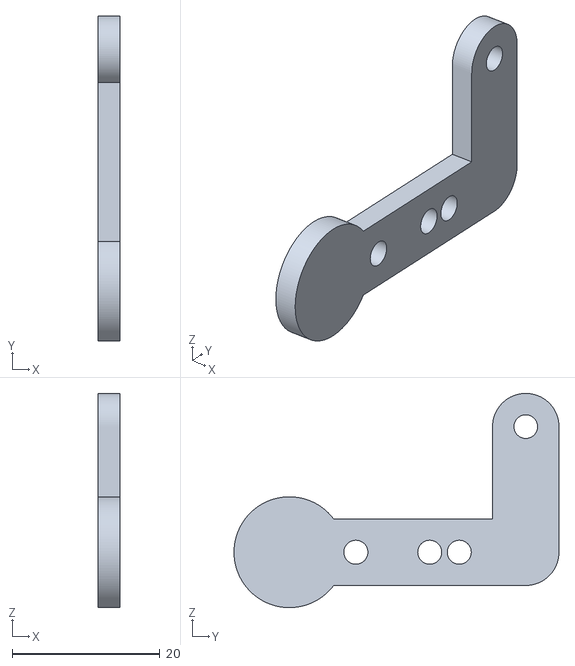
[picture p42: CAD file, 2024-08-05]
assets/3d-model/bucket/bucket_servoConnector.stl
3.00 x 44.0 x 29.0

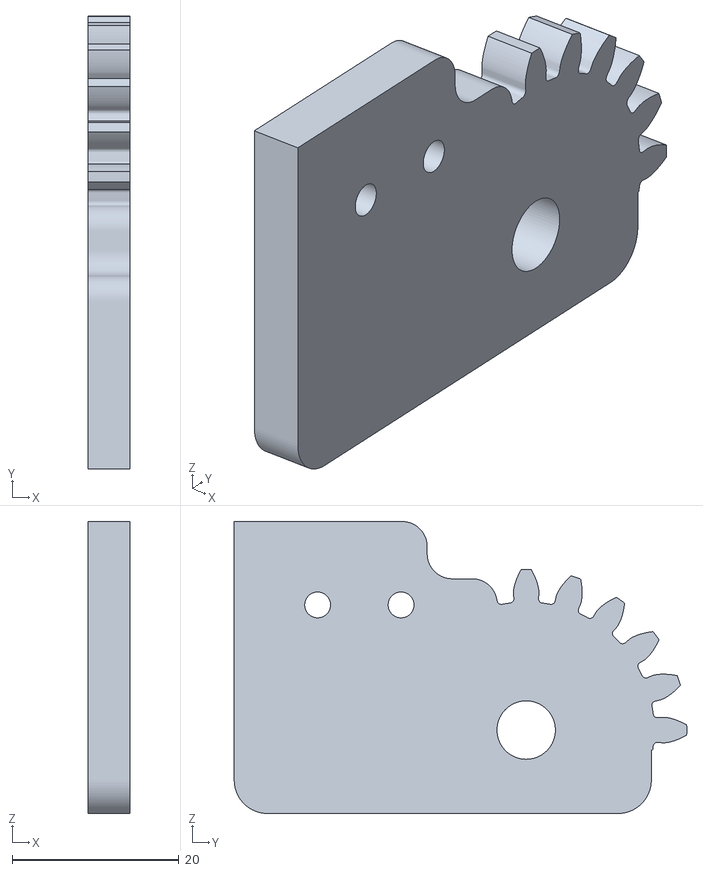
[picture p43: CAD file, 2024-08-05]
assets/3d-model/camera/camera_gearMount_left.stl
5.00 x 54.2 x 35.0

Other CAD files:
assets/3d-model/casing/frame_top.stl
assets/3d-model/other/slider_1.stl
assets/3d-model/arm/arm_right_1.stl
assets/3d-model/bucket/bucket_basePlate_right.stl
assets/3d-model/arm/arm_frame.stl
assets/3d-model/arm/arm_left_1.stl
assets/3d-model/arm/arm_left_2.stl
assets/3d-model/arm/arm_rodMount.stl
assets/3d-model/arm/arm_rod_left.stl
assets/3d-model/bucket/bucket.stl
assets/3d-model/camera/camera_basePlate_left.stl
assets/3d-model/camera/camera_basePlate_right.stl
assets/3d-model/camera/camera_frontGear.stl
assets/3d-model/camera/camera_gearConnector_outside_left.stl
assets/3d-model/camera/camera_gearConnector_outside_right.stl
assets/3d-model/camera/camera_middleGear.stl
assets/3d-model/camera/camera_mount.stl
assets/3d-model/camera/camera_servoConnector1.stl
assets/3d-model/camera/camera_servoConnector2.stl
assets/3d-model/casing/frame_right.stl
assets/3d-model/casing/frontPlate.stl
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

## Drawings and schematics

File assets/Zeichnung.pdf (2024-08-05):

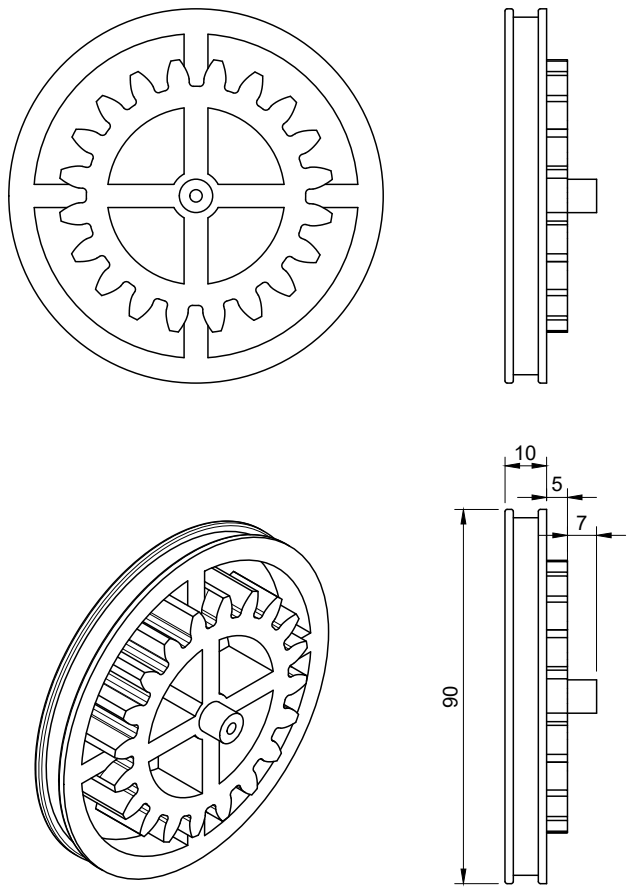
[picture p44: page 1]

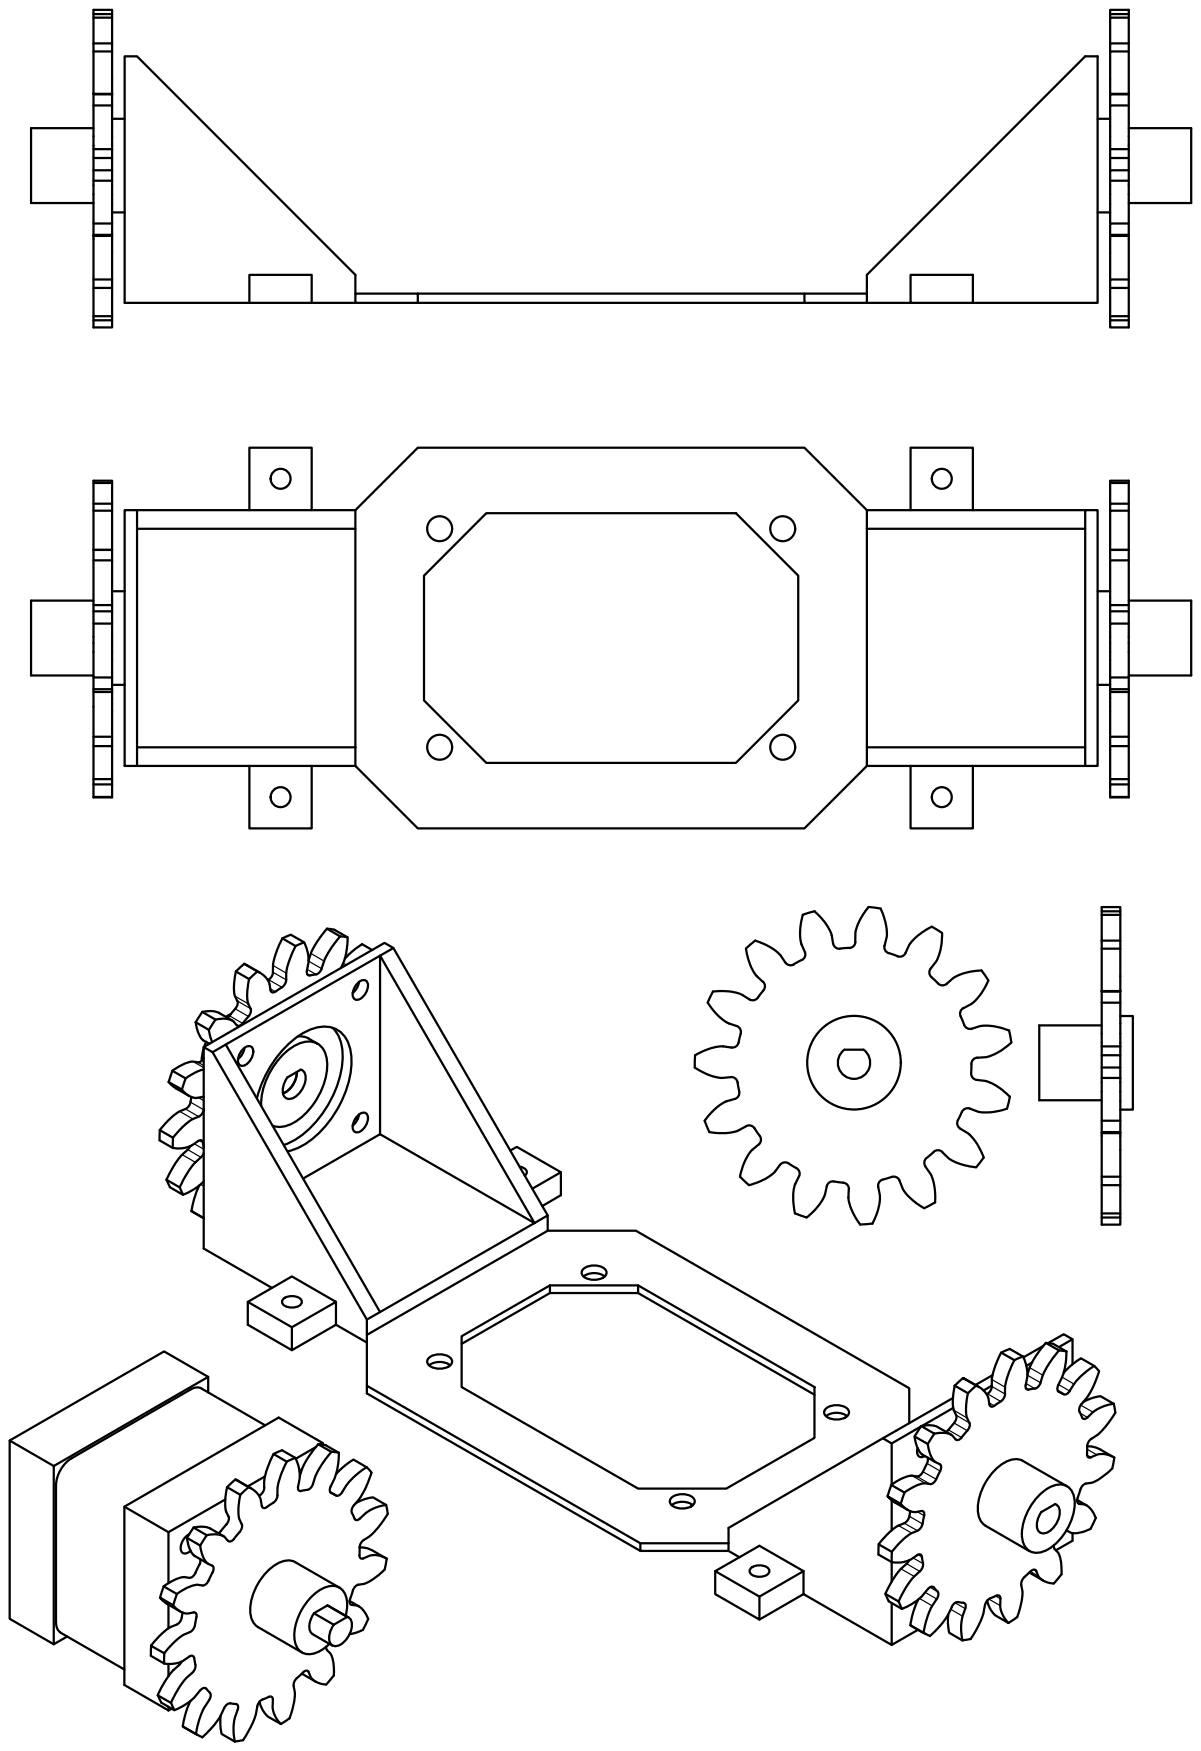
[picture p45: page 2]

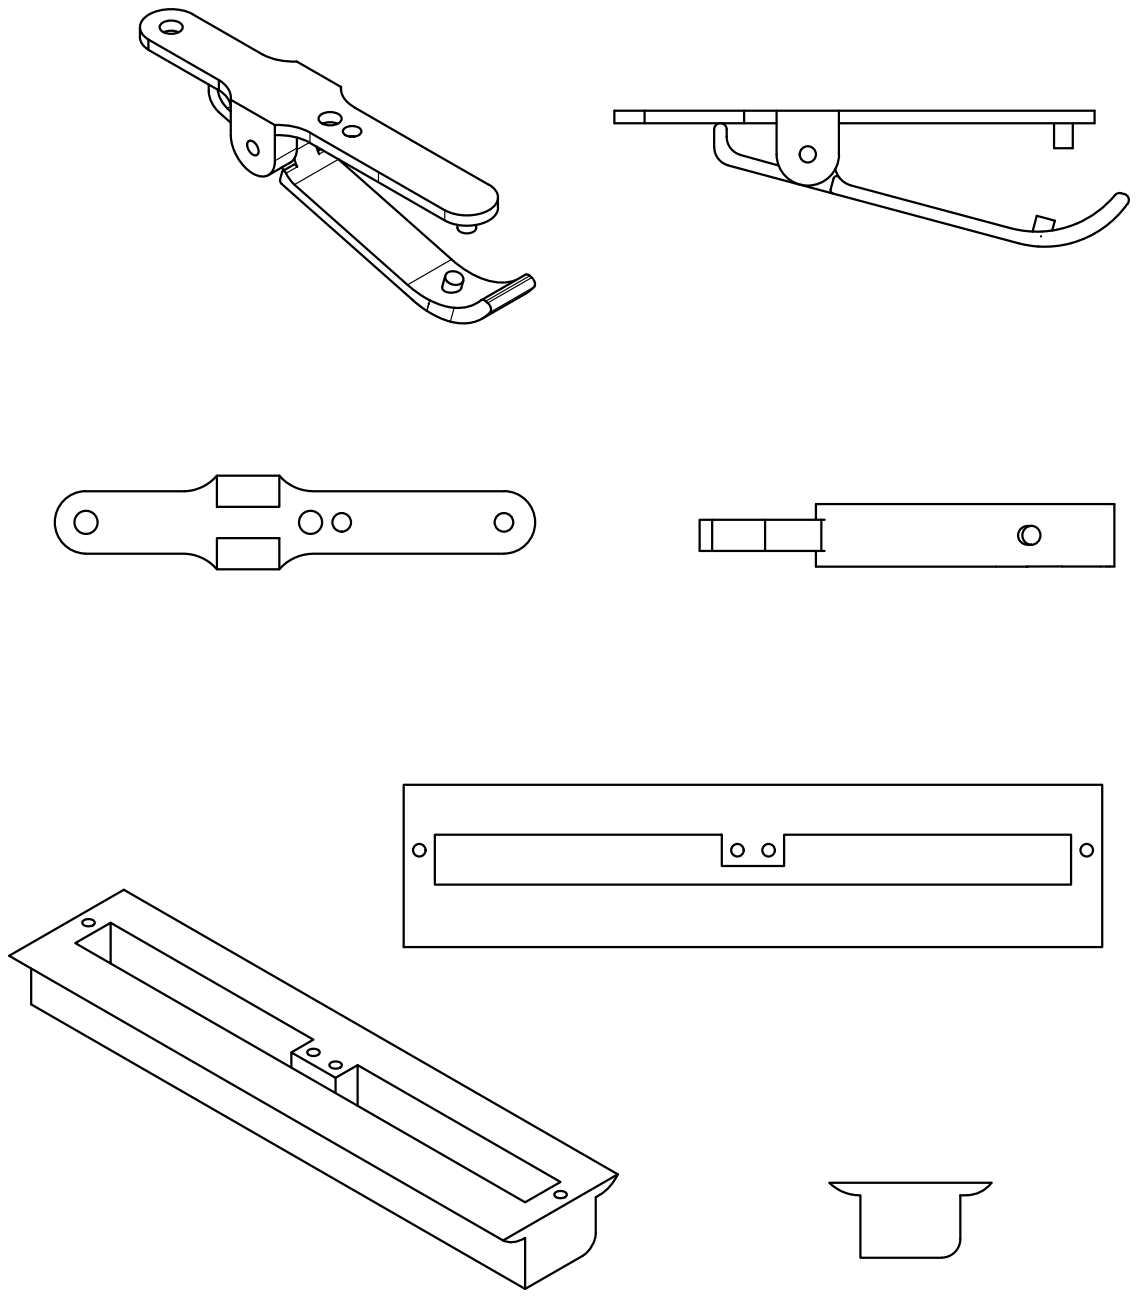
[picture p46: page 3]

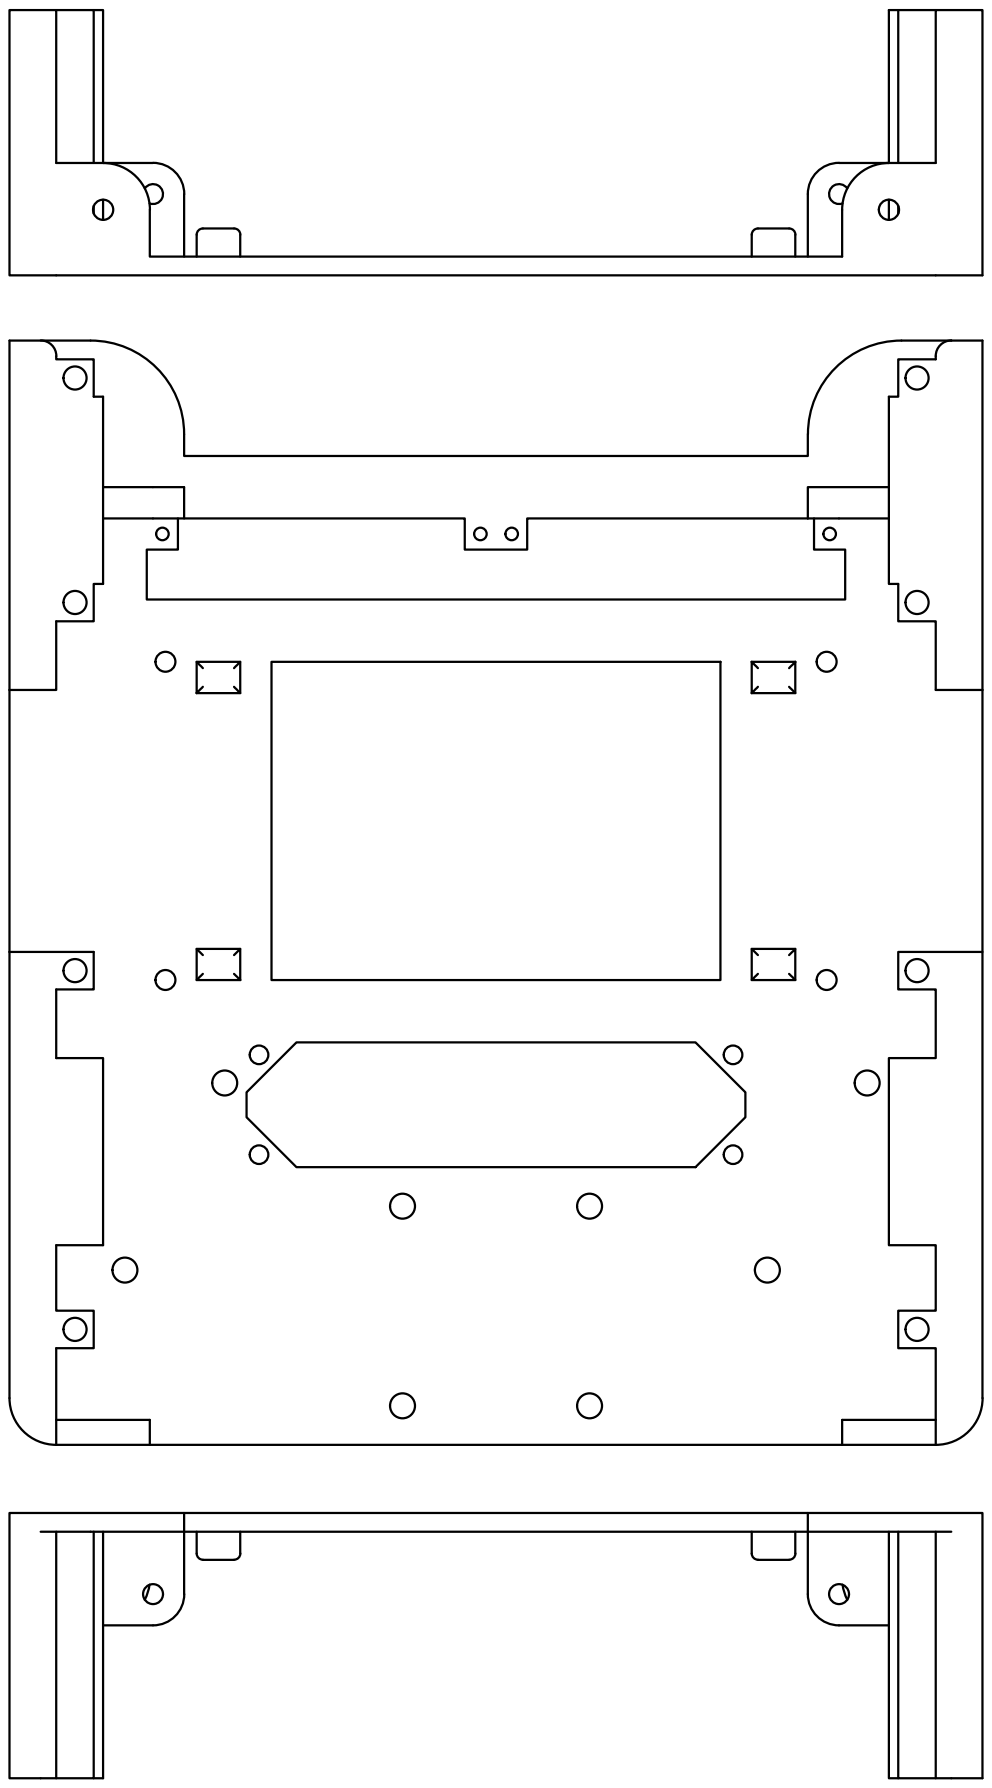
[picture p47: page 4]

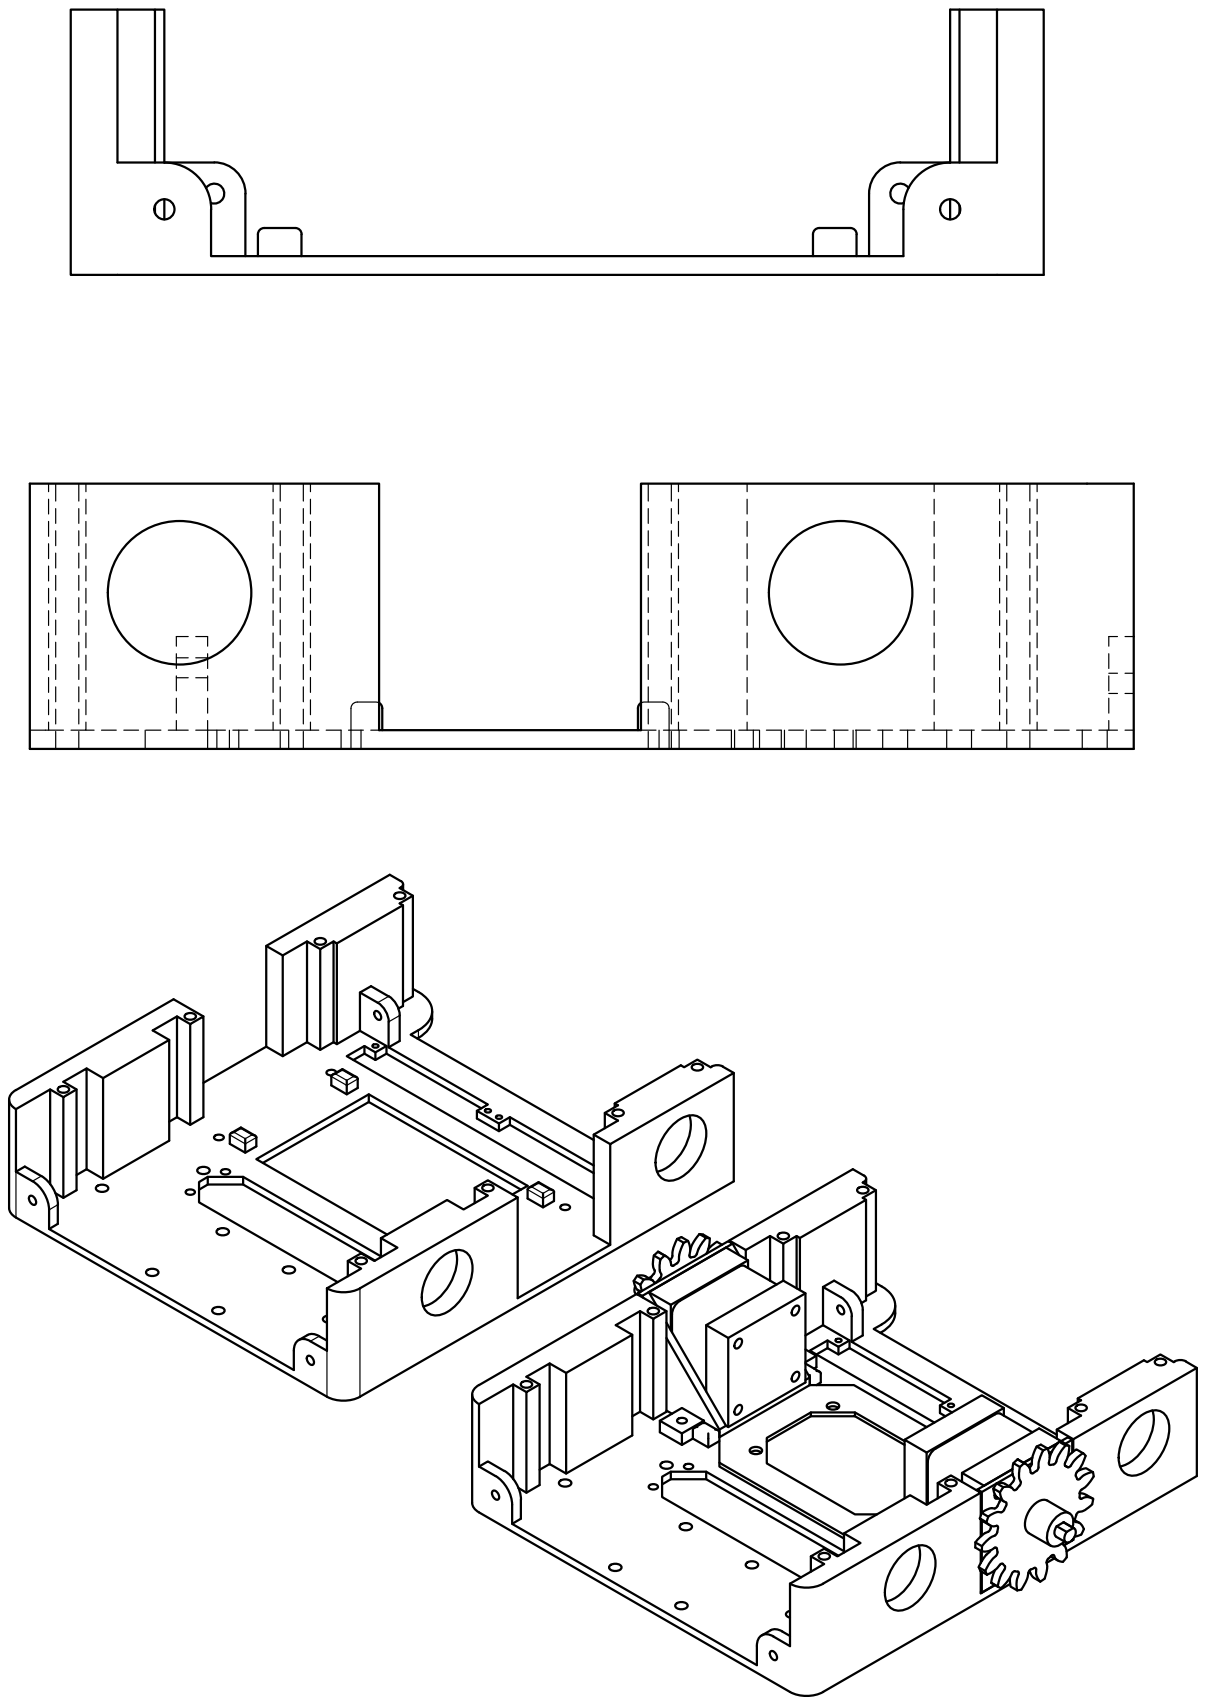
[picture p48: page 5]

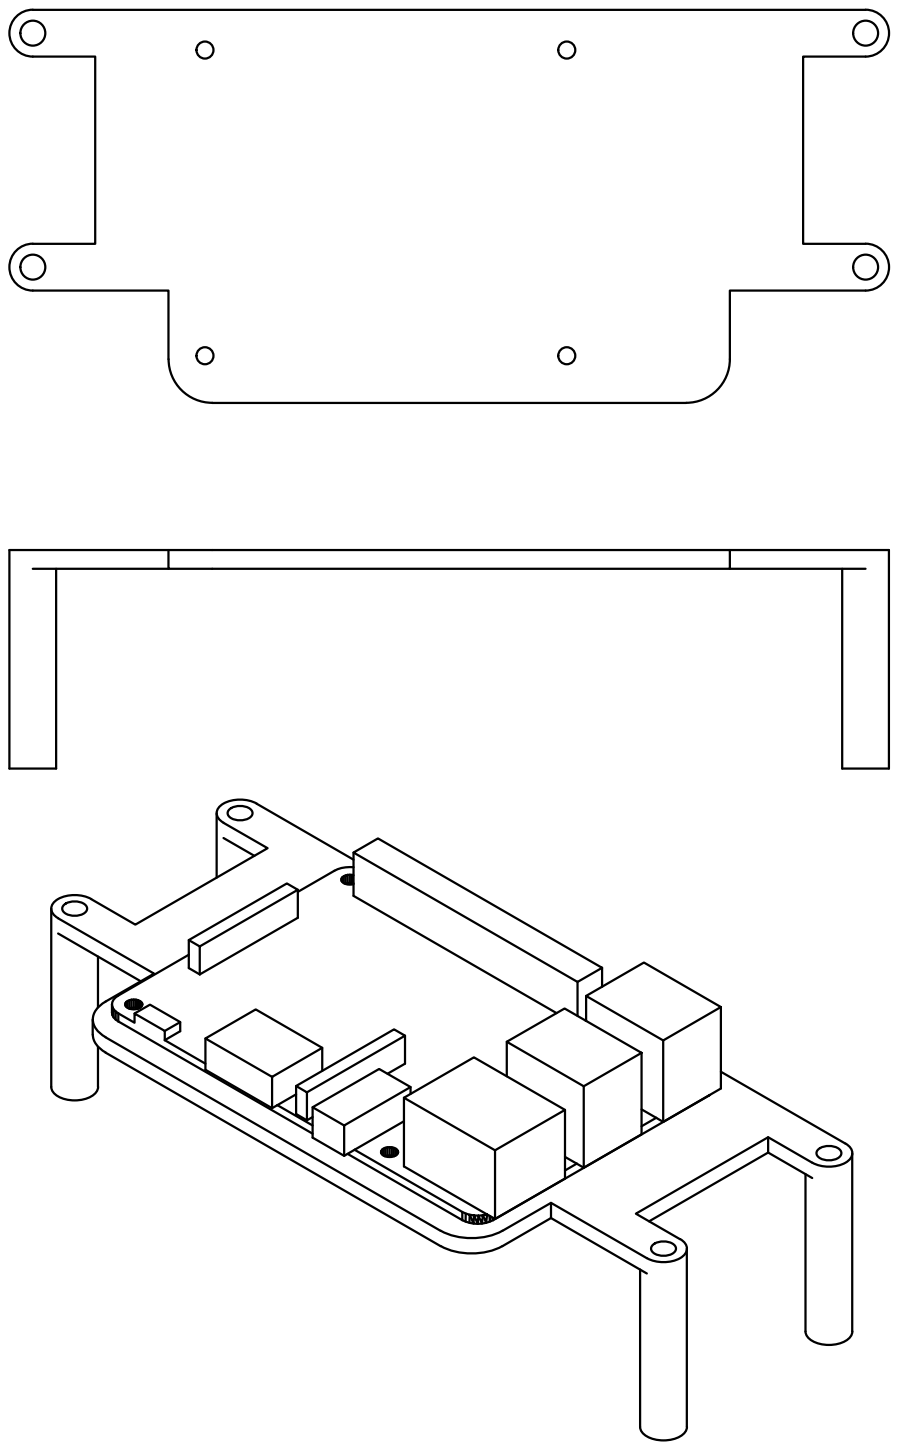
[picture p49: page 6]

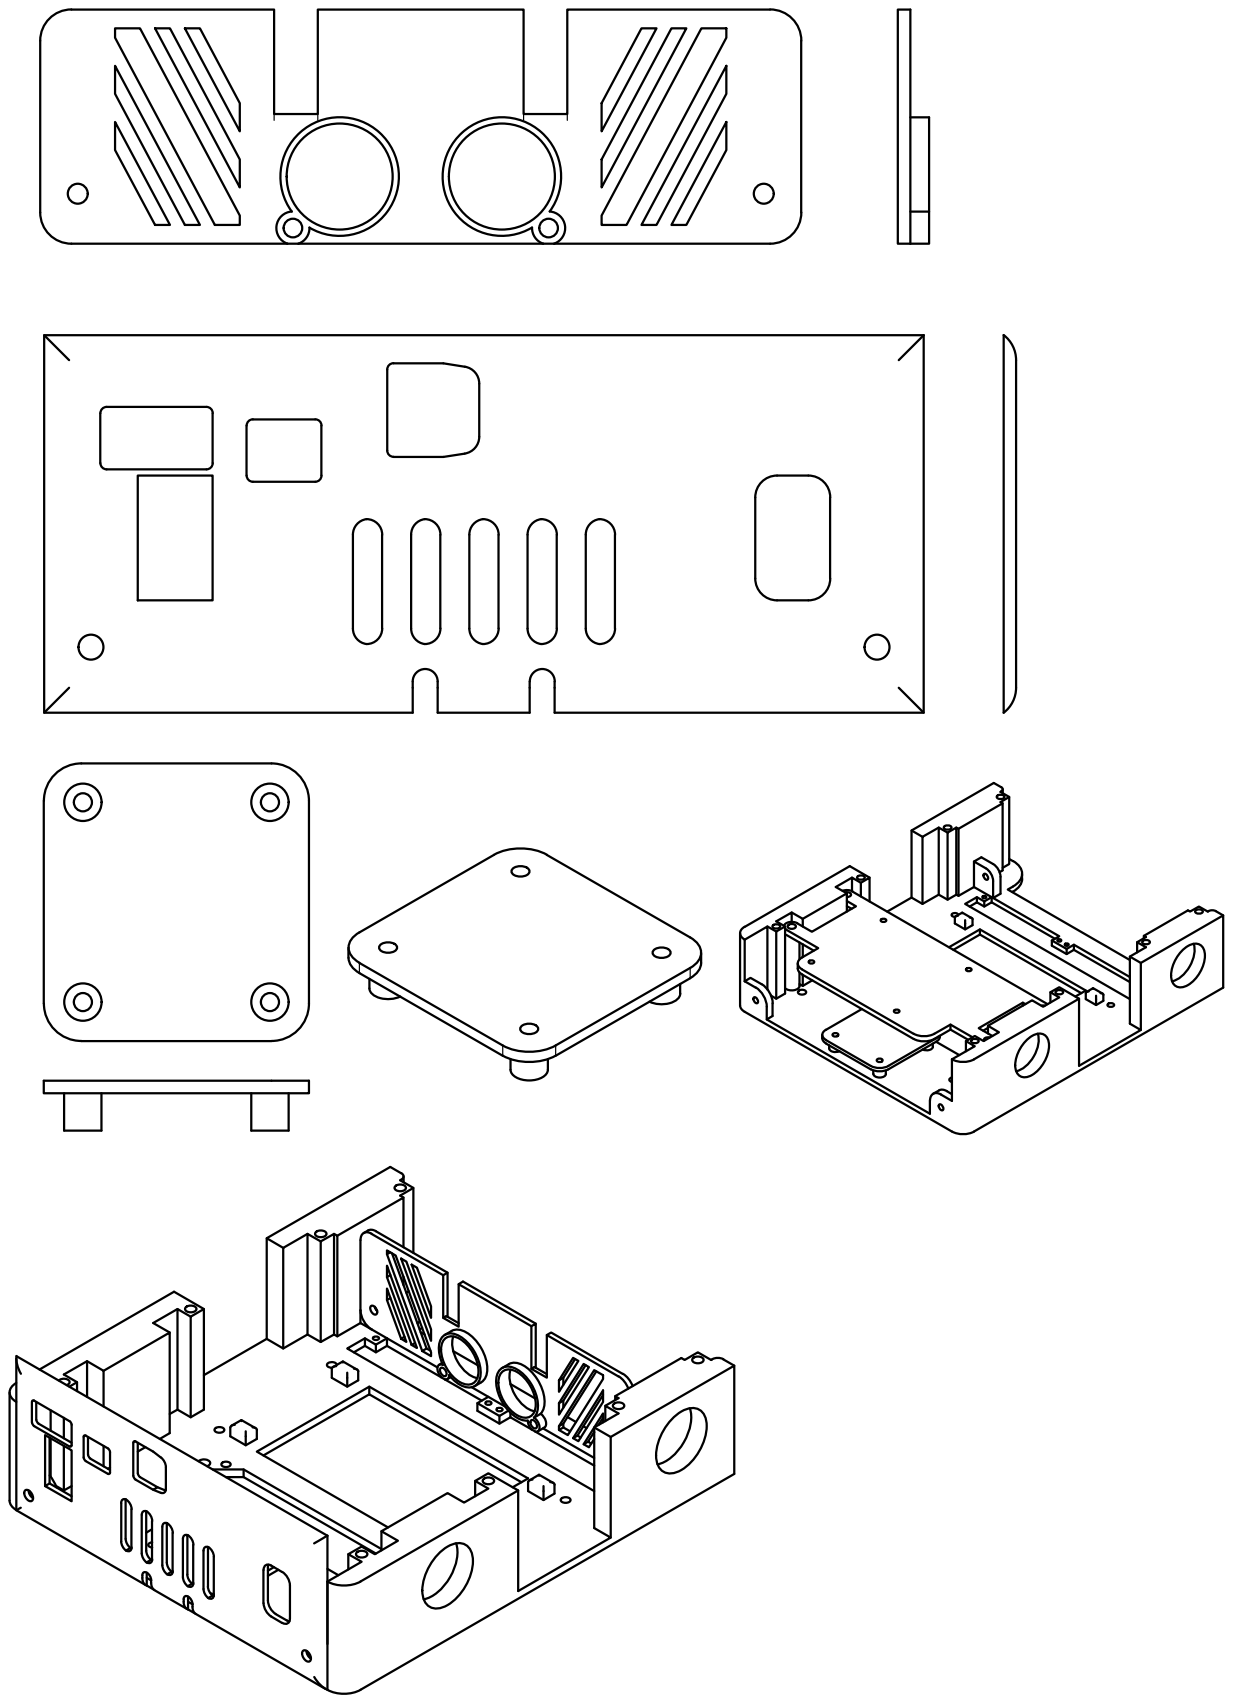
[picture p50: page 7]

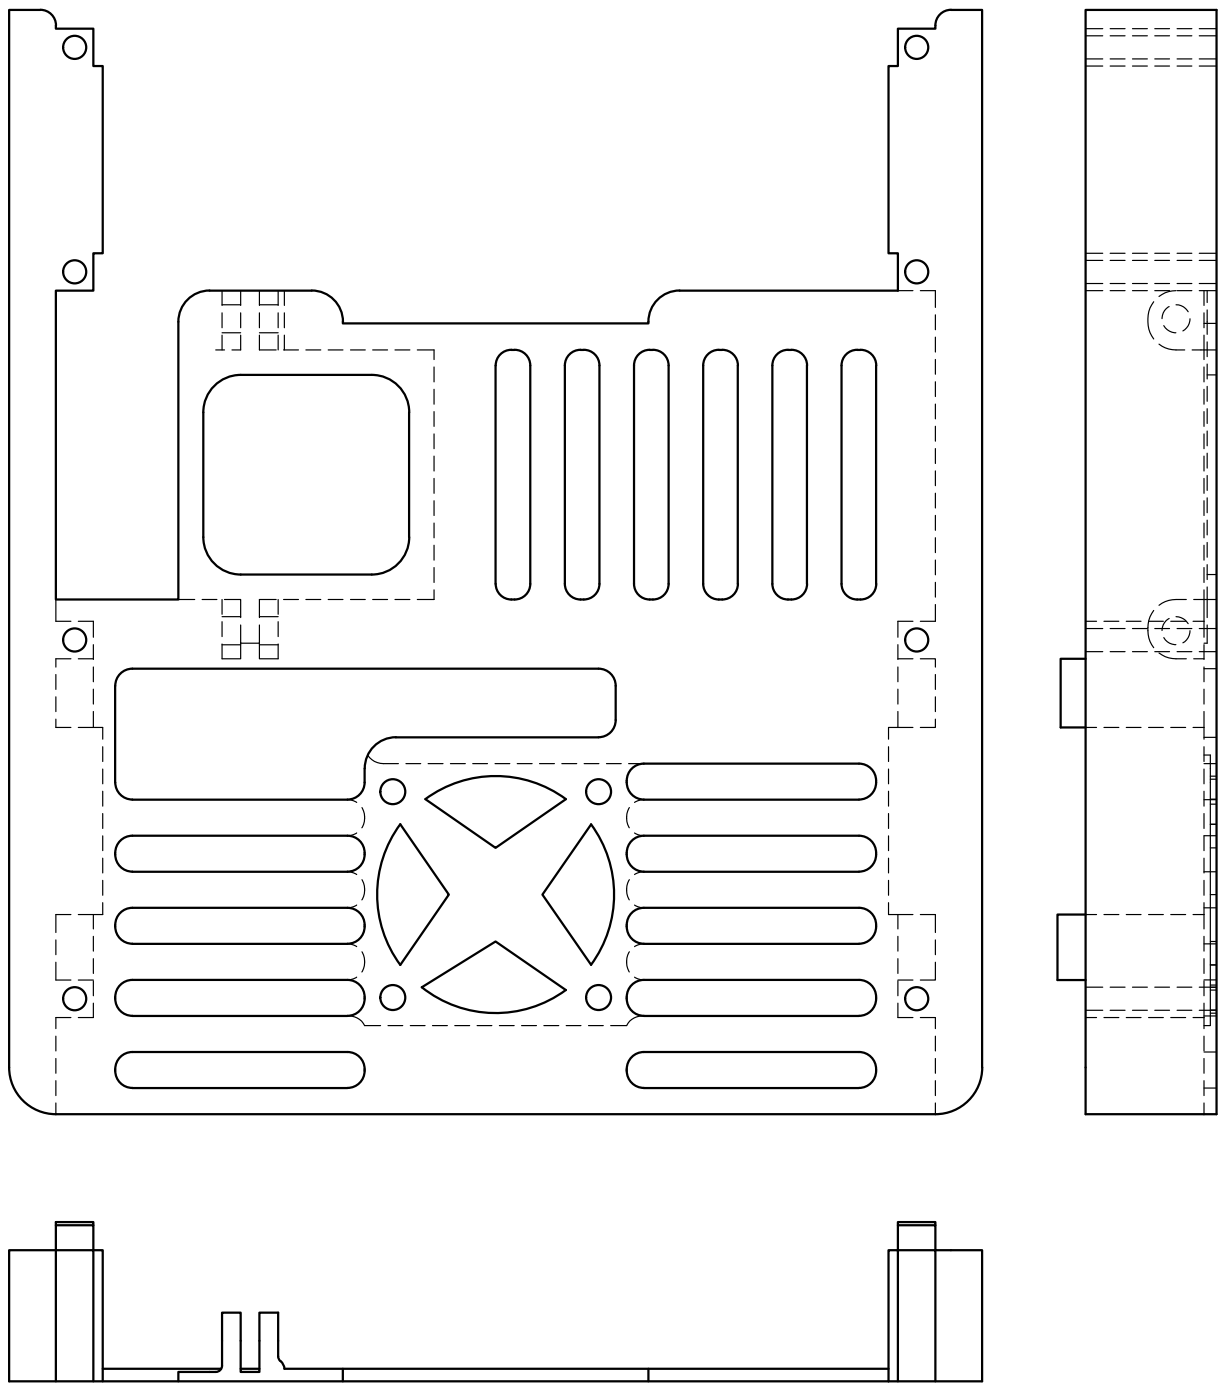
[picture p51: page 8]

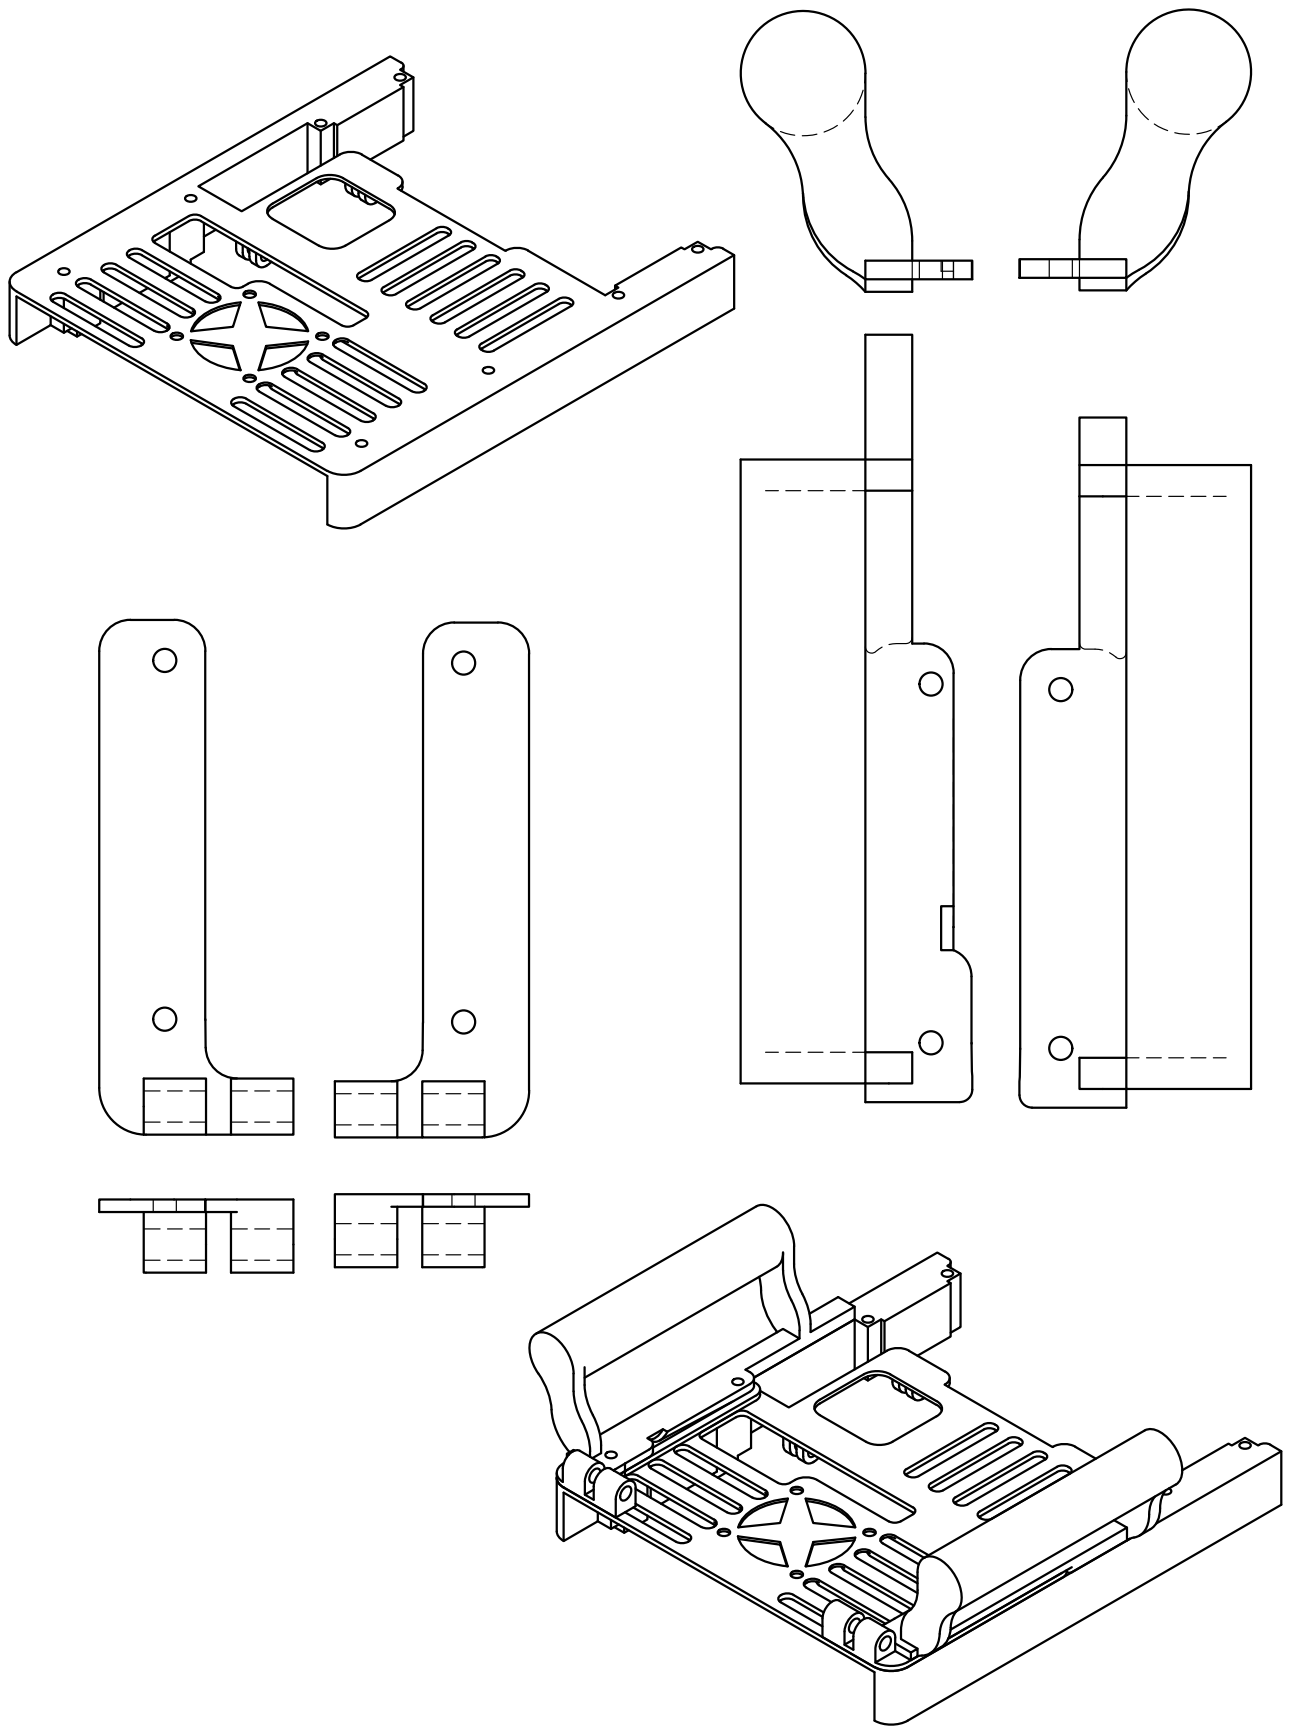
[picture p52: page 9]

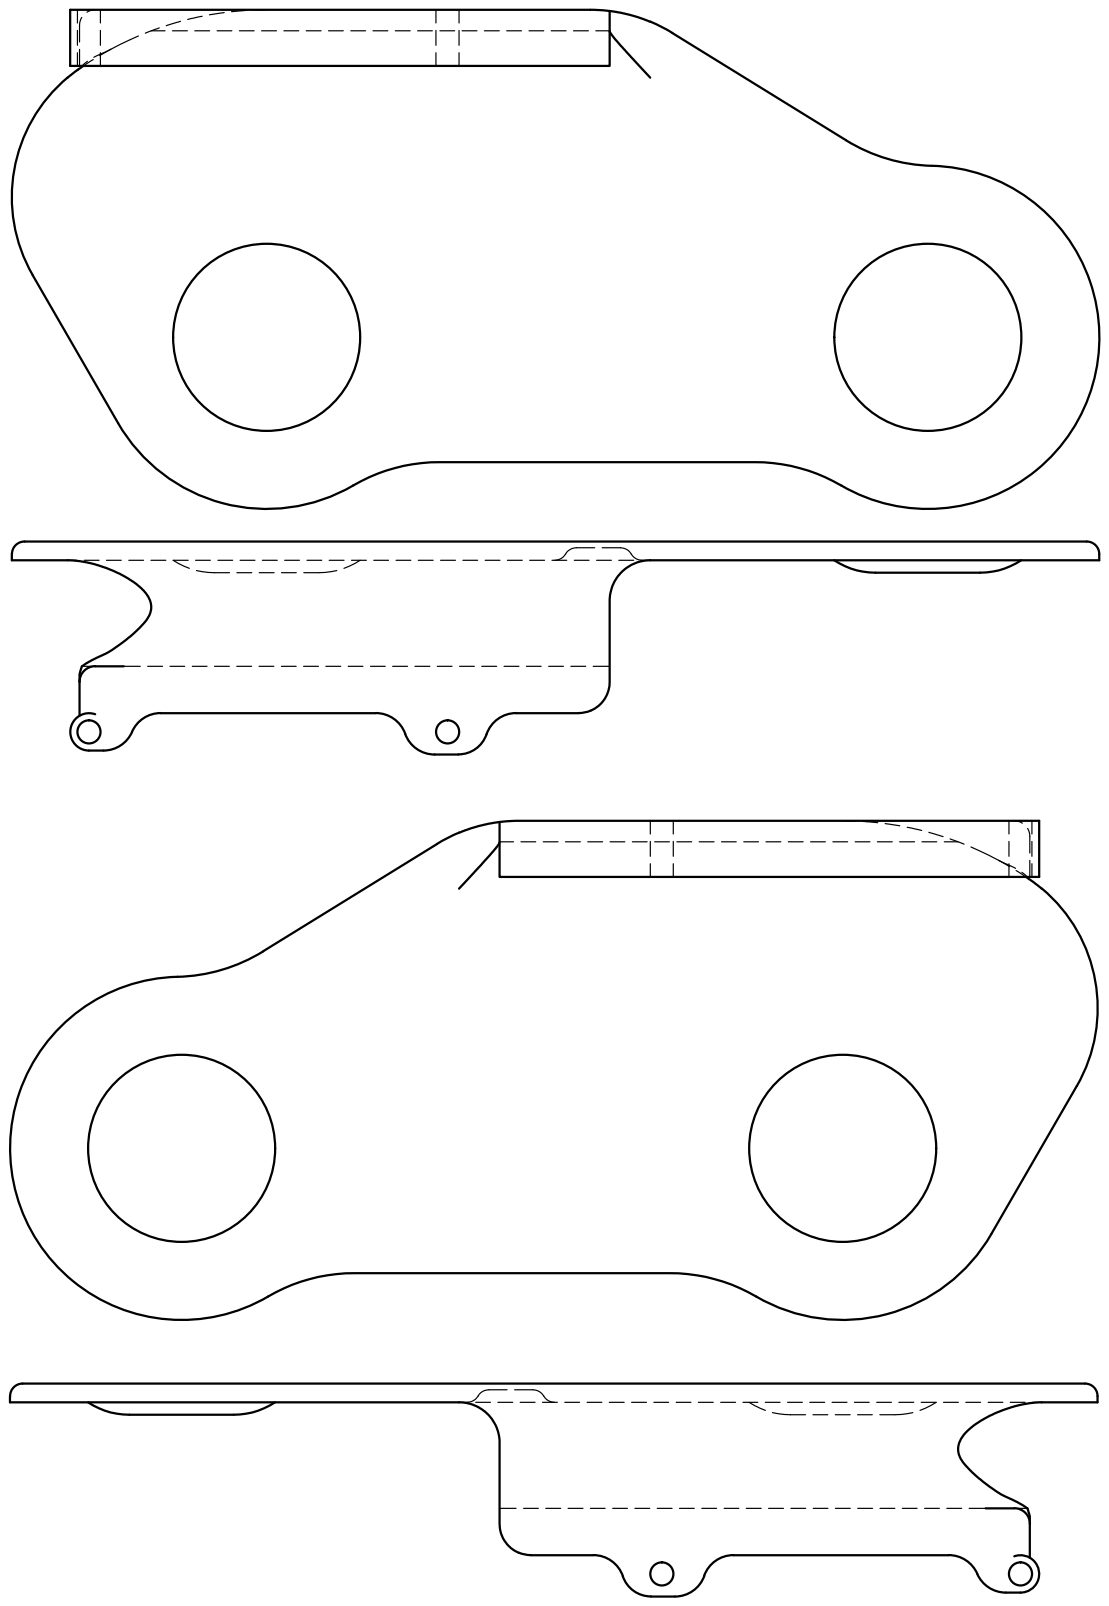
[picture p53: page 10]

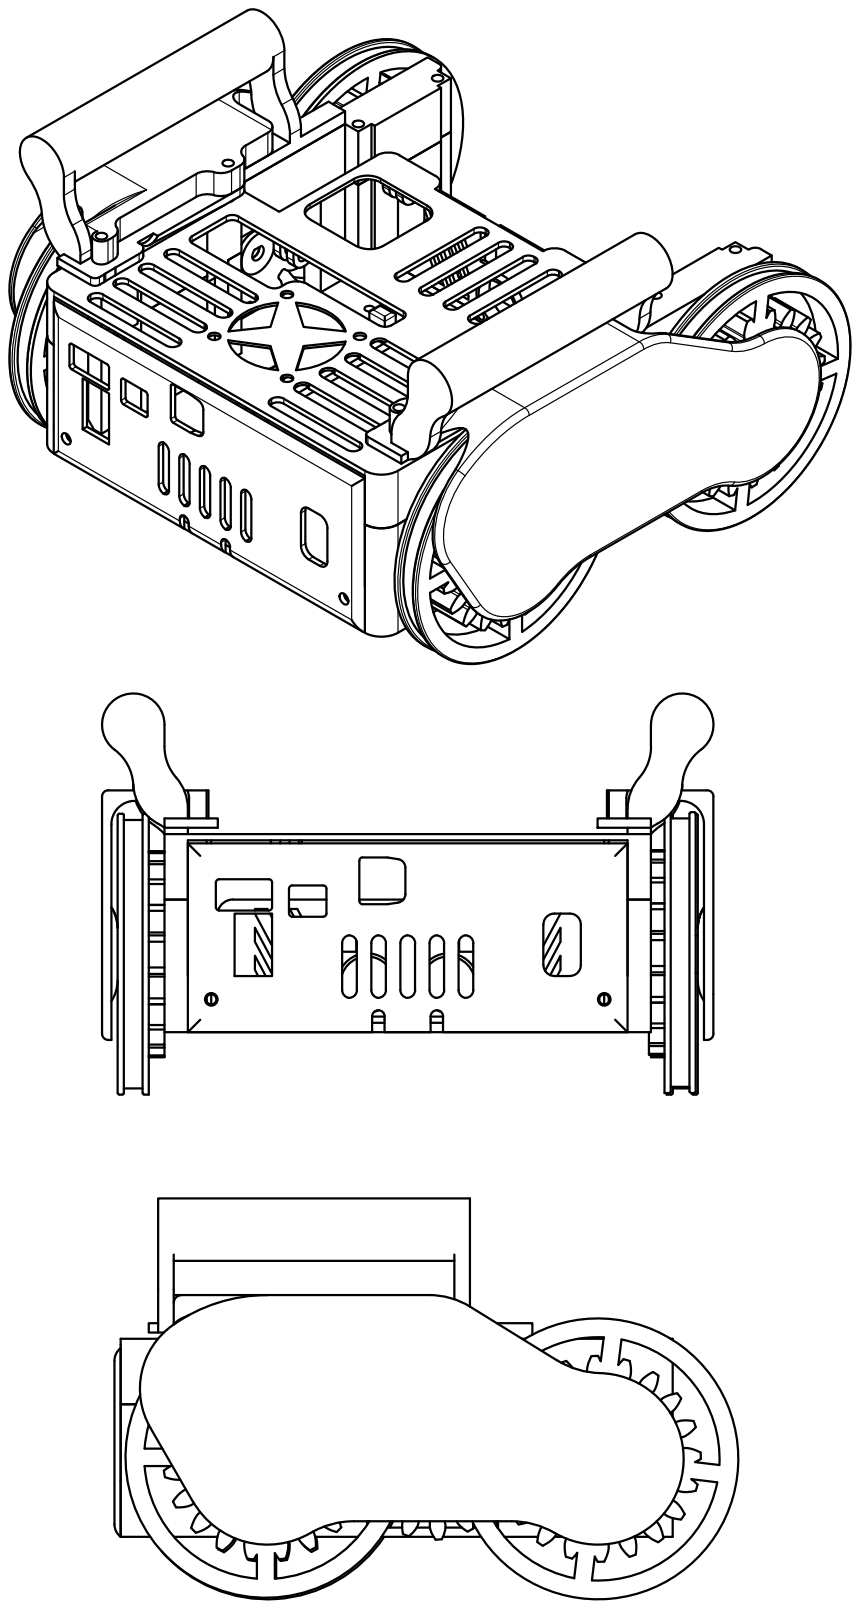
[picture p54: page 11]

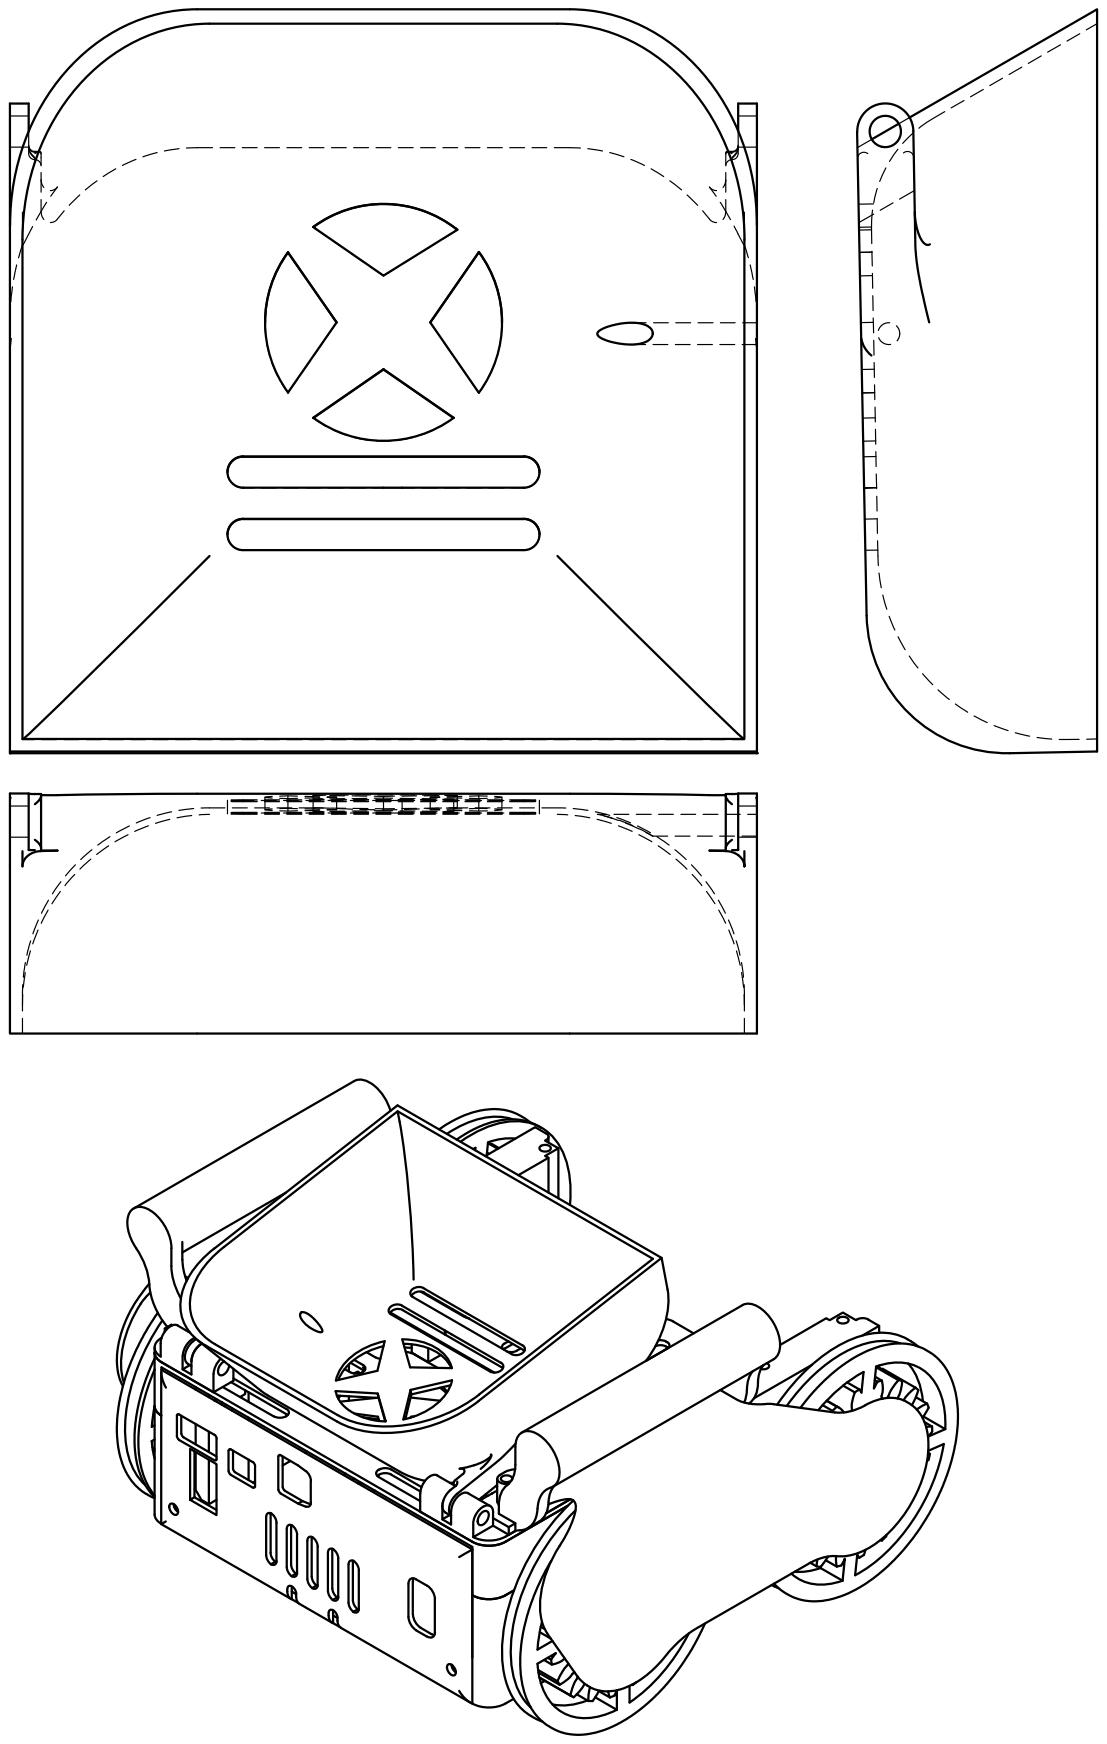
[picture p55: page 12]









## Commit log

2023-09-27 3d model entry
    [akku_mount.stl, back_plate.stl, big_Gear.stl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]
2024-05-01 Dokumentation (not complete yet)
    Erster Teil der Dokumentation
2024-05-01 Image Folder
    Verschiebung aller Bilder in "Image" zum Zwecke der Übersichtlichkeit
2024-08-05 Vervollständigung der Dokumentation
    [akku_mount.stl, arm_frame.stl, arm_left_1.stl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]
